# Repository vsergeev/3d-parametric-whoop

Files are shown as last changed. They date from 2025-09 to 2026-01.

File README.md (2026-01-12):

# Parametric Whoop

<table>
<tr>
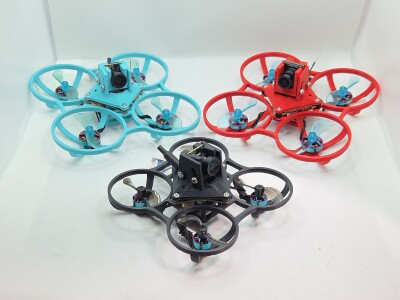
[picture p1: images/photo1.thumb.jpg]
<td></td>
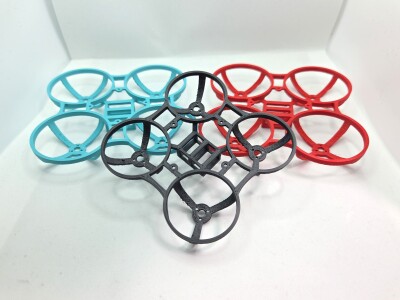
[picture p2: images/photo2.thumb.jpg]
<td></td>
</tr>
<tr>
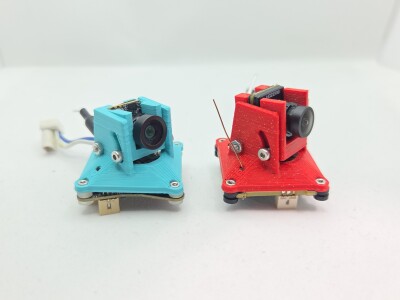
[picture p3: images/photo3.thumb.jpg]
<td></td>
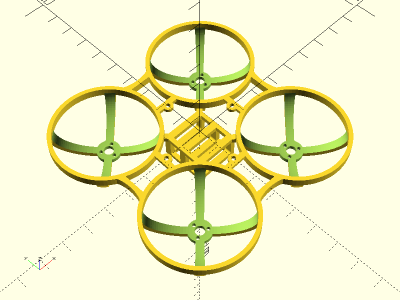
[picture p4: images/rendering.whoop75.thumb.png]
Whoop 75mm Rendering
<td></td>
</tr>
<tr>
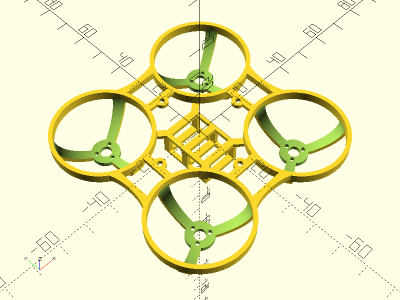
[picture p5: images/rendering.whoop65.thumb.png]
Whoop 65mm Rendering
<td></td>
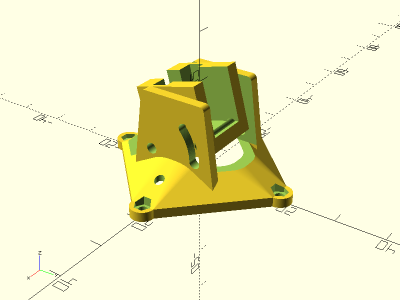
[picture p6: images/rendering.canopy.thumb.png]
Canopy Rendering
<td></td>
</tr>
</table>

A parametric whoop frame and canopy. Canopy has an adjustable camera tilt of 0 to 40 degrees, secured with two M2 bolts. Canopy mounts to the frame with M1.4 bolts and captured nuts. Example builds for 75mm and 65mm analog and digital whoops provided. Made with OpenSCAD.

Strong impacts may break the motor struts, but they are easily fixed with CA and then stronger than before. Check out the [Parametric Toothpick Frame](https://github.com/vsergeev/3d-parametric-toothpick) and [Parametric Whoop Canopy](https://github.com/vsergeev/3d-parametric-whoop-canopy) projects for more durable designs.

**Base Designs**

* [`whoop.scad`](whoop.scad) - Whoop Frame
* [`canopy.scad`](canopy.scad) - Whoop Canopy

**Instances**

* [`75mm_26x26_whoop.scad`](75mm_26x26_whoop.scad) - 75mm Whoop Frame with 26mm mounting holes (weight 8.0g ASA)
* [`65mm_26x26_whoop.scad`](65mm_26x26_whoop.scad) - 65mm Whoop Frame with 26mm mounting holes (weight 4.8g ASA)
* [`betafpv_c03_26x26_canopy.scad`](betafpv_c03_26x26_canopy.scad) - Canopy for BETAFPV C03 Camera with 26mm mounting holes (weight 1.7g ASA)
* [`betafpv_c03_camera_harness.scad`](betafpv_c03_camera_harness.scad) - BETAFPV C03 Camera Harness (weight 1.2g ASA)
* [`hdzero_lux_26x26_canopy.scad`](hdzero_lux_26x26_canopy.scad) - Canopy for HDZero Lux Camera with 26mm mounting holes (weight 1.8g ASA)
* [`hdzero_lux_camera_harness.scad`](hdzero_lux_camera_harness.scad) - HDZero Lux Camera Harness (weight 1.6g ASA)

**Recommended Print Settings:** ASA / PETG / Hard TPU, 0.20mm layer height, 100% infill, supports on build plate only for whoop frame, no supports for canopy or camera harness

**Recommended Support Settings (PrusaSlicer):** Avoid Crossing Perimeters: True, Style: Snug, Top contact Z distance: 0.20 (ASA), 0.23 (PETG), 0.25 (Hard TPU), Pattern Spacing: 3mm, Top interface layers: 4, XY separation between an object and its support: 100% (ASA, PETG), 250% (Hard TPU)

**Printables**: https://www.printables.com/model/1402069-parametric-whoop

**Thingiverse**: https://www.thingiverse.com/thing:7133627

## Builds

### 75mm BETAFPV Matrix 1S 5in1 (Analog VTX) + BETAFPV C03 Camera

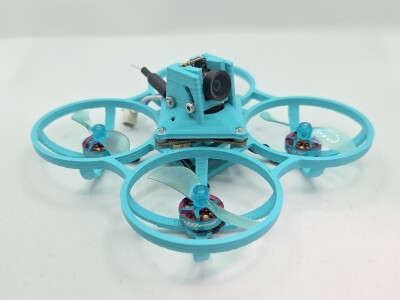
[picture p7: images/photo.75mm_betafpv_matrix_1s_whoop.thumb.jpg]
75mm BETAFPV Matrix 1S Whoop


* Frame: [75mm_26x26_whoop.stl](stl/75mm_26x26_whoop.stl)
* Canopy: [betafpv_c03_26x26_canopy.stl](stl/betafpv_c03_26x26_canopy.stl)
* Camera Harness: [betafpv_c03_camera_harness.stl](stl/betafpv_c03_camera_harness.stl)
* Flight Controller: [BETAFPV Matrix 1S](https://betafpv.com/collections/brushless-flight-controller/products/matrix-1s-brushless-flight-controller)
* Camera: [BETAFPV C03 Camera](https://betafpv.com/products/c03-fpv-micro-camera)
* Motors: RCinPower GTS V3 1002 19000KV
* Props: Gemfan 1610-2 40mm
* Hardware:
    * 12x M1.4x3 for motors (included with motors)
    * 4x M1.4 nuts and 4x M1.4x8 bolts for frame, flight controller, canopy
    * 2x M2 nuts and 2x M2x20 bolts for camera harness

Total Weight without battery: 31.8g ASA

### 65mm BETAFPV Matrix 1S 5in1 (Analog VTX) + BETAFPV C03 Camera

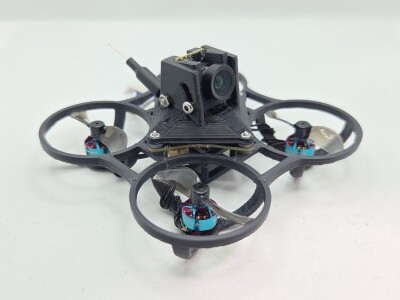
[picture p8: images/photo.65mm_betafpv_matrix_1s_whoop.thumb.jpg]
65mm BETAFPV Matrix 1S Whoop


* Frame: [65mm_26x26_whoop.stl](stl/65mm_26x26_whoop.stl)
* Canopy: [betafpv_c03_26x26_canopy.stl](stl/betafpv_c03_26x26_canopy.stl)
* Camera Harness: [betafpv_c03_camera_harness.stl](stl/betafpv_c03_camera_harness.stl)
* Flight Controller: [BETAFPV Matrix 1S](https://betafpv.com/collections/brushless-flight-controller/products/matrix-1s-brushless-flight-controller)
* Camera: [BETAFPV C03 Camera](https://betafpv.com/products/c03-fpv-micro-camera)
* Motors: RCinPower 0702 27000KV
* Props: Gemfan 1210-2 31mm
* Hardware:
    * 12x M1.4x3 for motors (included with motors)
    * 4x M1.4 nuts and 4x M1.4x8 bolts for frame, flight controller, canopy
    * 2x M2 nuts and 2x M2x20 bolts for camera harness

Total Weight without battery: 24.4g ASA

### 75mm HDZero AIO5 (Digital VTX) + HDZero Lux Camera

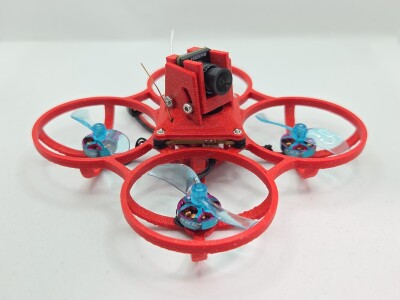
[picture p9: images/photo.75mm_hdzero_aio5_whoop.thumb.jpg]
75mm HDZero AIO5 Whoop


* Frame: [`75mm_26x26_whoop.scad`](75mm_26x26_whoop.scad) with `battery_cage_y_length = 16;`
* Canopy: [hdzero_lux_26x26_canopy.stl](stl/hdzero_lux_26x26_canopy.stl)
* Camera Harness: [hdzero_lux_camera_harness.stl](stl/hdzero_lux_camera_harness.stl)
* Flight Controller: [HDZero AIO5](https://www.hd-zero.com/product-page/hdzero-aio5)
* Camera: [HDZero Lux Camera](https://www.hd-zero.com/product-page/hdzero-lux-camera)
* Motors: RCinPower GTS V3 1002 19000KV
* Props: Gemfan 1610-2 40mm
* Hardware:
    * 12x M1.4x3 for motors (included with motors)
    * 4x M1.4 nuts and 4x M1.4x8 bolts for frame, flight controller, canopy
    * 2x M2 nuts and 2x M2x20 bolts for camera harness

Total Weight without battery: 35.2g ASA

## License



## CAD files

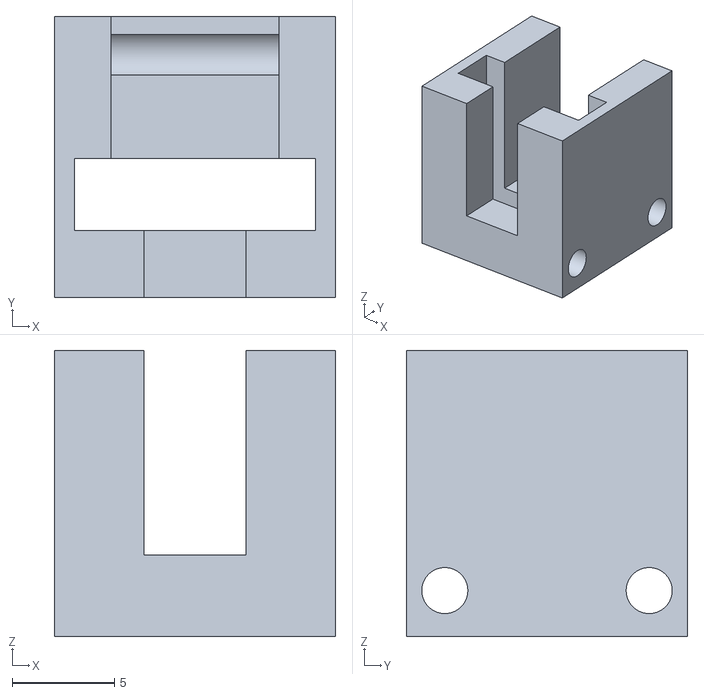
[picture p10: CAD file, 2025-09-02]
stl/betafpv_c03_camera_harness.stl
13.8 x 13.8 x 14.0

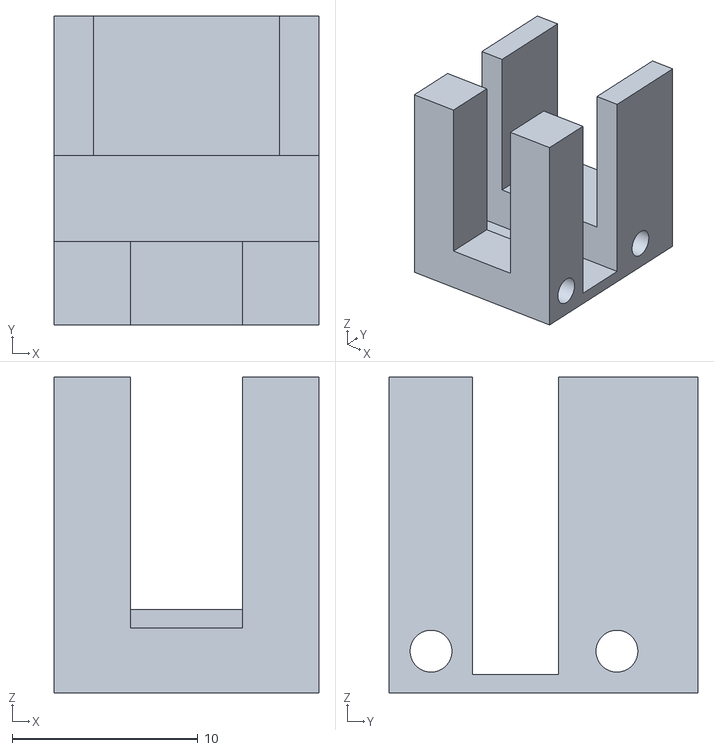
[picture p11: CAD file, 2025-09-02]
stl/hdzero_lux_camera_harness.stl
14.2 x 16.6 x 17.0

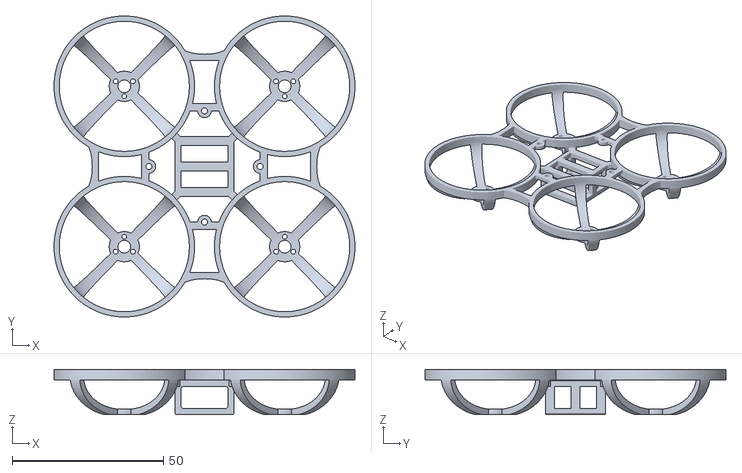
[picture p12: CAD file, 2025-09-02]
stl/75mm_26x26_whoop.stl
99.5 x 99.5 x 15.0

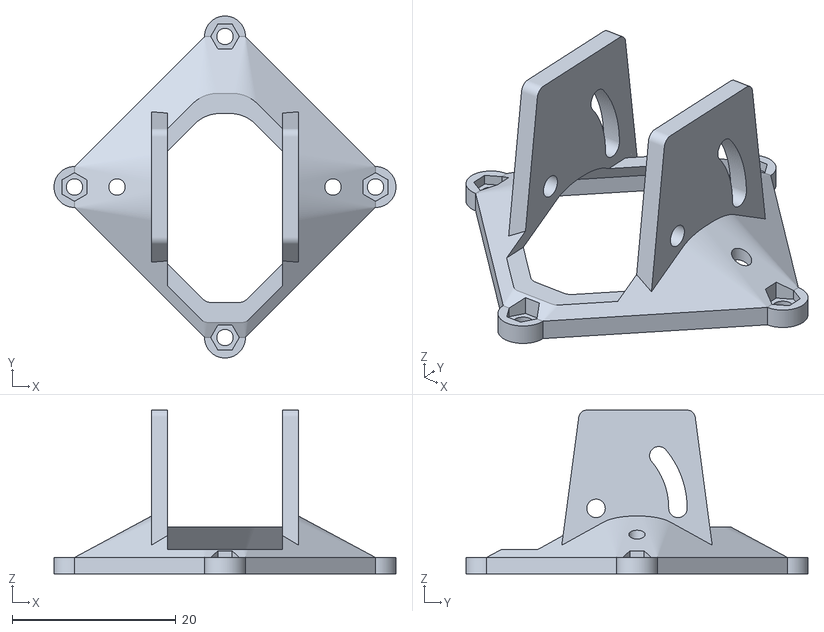
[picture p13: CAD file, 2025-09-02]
stl/betafpv_c03_26x26_canopy.stl
41.8 x 41.8 x 20.0

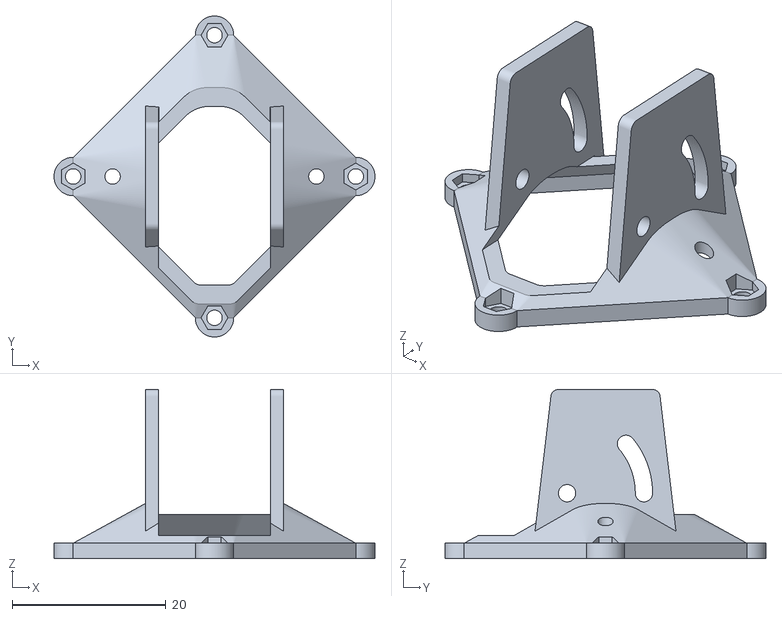
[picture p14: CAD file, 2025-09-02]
stl/hdzero_lux_26x26_canopy.stl
41.8 x 41.8 x 22.0

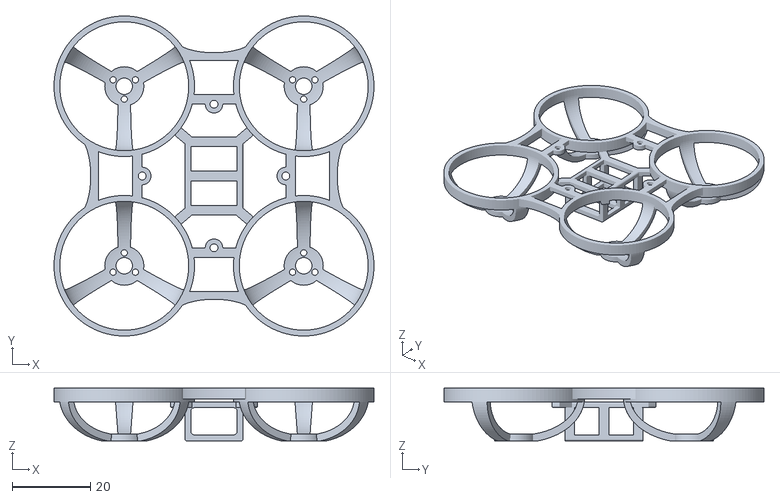
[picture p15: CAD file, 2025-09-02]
stl/65mm_26x26_whoop.stl
82.0 x 82.0 x 13.5

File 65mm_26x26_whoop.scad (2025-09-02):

include <whoop.scad>;

// Dimensional changes
whoop_xy_wheelbase = 65;
motor_cage_xy_diameter = 33;
motor_cage_z_depth = 13.5;
battery_cage_xz_dimensions = [11.9, 7.0];

// Weight savings overrides
motor_cage_strut_count = 3;
motor_cage_strut_z_angle = 0;
motor_base_z_thickness = 1.5;
motor_cage_xyz_thickness = 1.5;
motor_cage_loop_z_thickness = 2.75;
crossbar_z_thickness = 2.75;
battery_cage_xz_thickness = 1.5;
battery_cage_bracket_y_thickness = 2.5;

whoop();

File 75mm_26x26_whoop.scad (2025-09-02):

include <whoop.scad>;

// Default parameters are for 75mm whoop

whoop();

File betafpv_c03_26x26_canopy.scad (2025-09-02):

include <canopy.scad>;

// Default parameters are for BETAFPV C03 Camera Harness

canopy();

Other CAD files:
betafpv_c03_camera_harness.scad
canopy.scad
hdzero_lux_26x26_canopy.scad
hdzero_lux_camera_harness.scad
whoop.scad

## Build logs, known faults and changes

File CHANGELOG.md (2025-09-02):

* v1.0 - 09/01/2025
    * Initial release.

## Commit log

2025-09-02 add printables and thingiverse links to readme
2026-01-12 add link to new frame and canopy projects

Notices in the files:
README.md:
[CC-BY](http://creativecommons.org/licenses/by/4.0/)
